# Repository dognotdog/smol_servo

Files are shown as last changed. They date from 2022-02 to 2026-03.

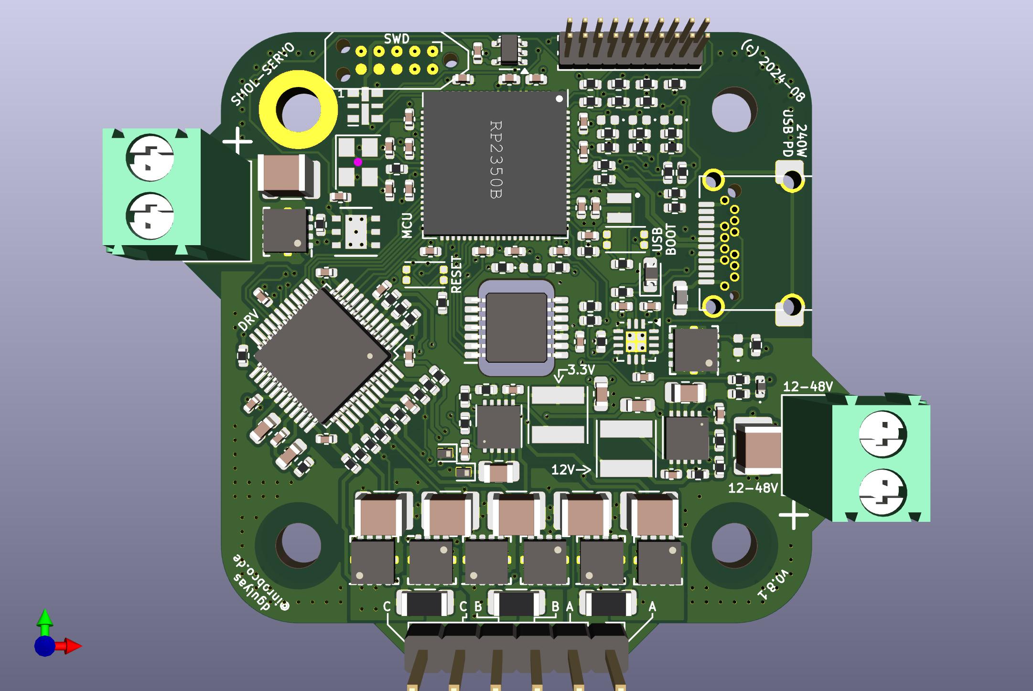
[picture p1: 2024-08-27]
hardware/smol-servo-rpi2350-tmc6200/smol-servo-rpi2350-tmc6200.jpg

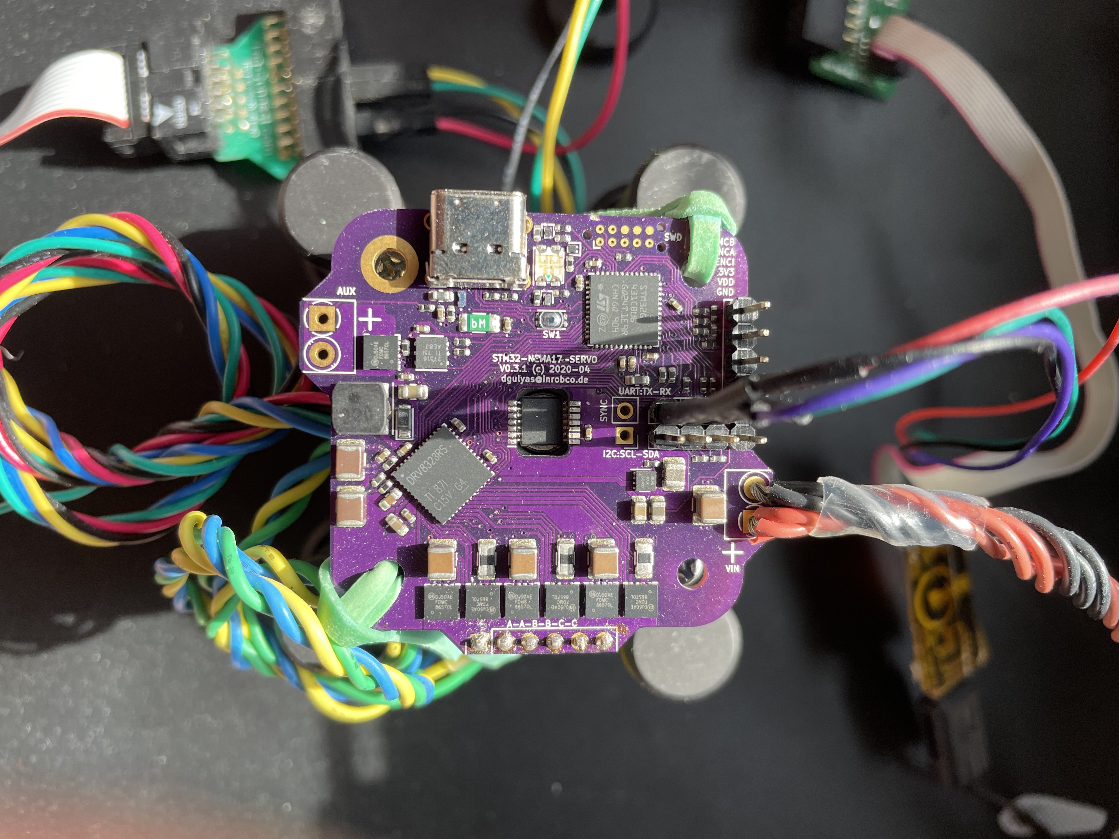
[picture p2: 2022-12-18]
doc/v0.3.1_proto.jpg

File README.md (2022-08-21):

# Project Layout

## firmware48

Contains files specific to 48pin STM32G431 on the stm32-nema17-servo board.

## mechaduino-firmware

Firmware for Mechaduino's SAMD21G18A Cortex M0+.

## hardware

Hardware design files for Schematic and PCB.

## tests

There is a basic harness in place to use [Unity](https://github.com/ThrowTheSwitch/Unity) for unit testing. Create `foo_test.c` modules for testing, and `foo_test.mk` makefiles for additional setup.

# Calculations

### Current Sense Shunt Resistor Value

Rated continous current 8A, max. Bus Voltage 50V, min. load 1R

 - 1206 can dissipate 1.5W usually, using a conservative 1W for the rated current: P/I^2 -> Rs < 15.6mOhm

With a 1R load on a 50V bus, up to 50A could flow at once, but hopefully motor inductance smoothes that out. Assuming 50kHz, 2mH winding inductance:
	V = L * di/dt -> di/dt = V/L = 25kA/s @ 50kHz = 0.5 A/cycle

### Gate Drive

The required charge pump current is
	I_VCP = 3 * Q_G * f_PWM.

DRV8323 charge pump VBUS limits:
6V -> 10mA
8V -> 15mA
10V -> 20mA
13V -> 25mA

#### NTTFS4937N

Q_G = 35.5 nC

I_VCP = 3.55 mA @ 100kHz
I_VCP = 1.78 mA @ 50kHz

Charge pump current capacity is well over required charge pump current.

#### FDMC86570L

Q_G < 88 nC

I_VCP = 8.8 mA @ 100kHz
I_VCP = 4.4 mA @ 50kHz

#### FDMC86183

Q_G ~ 15 nC
Q_gd ~ 3.4 nC

### Passive NSS OR circuit

3.3V, 5pF gate capacitance, 8mA sink/source per pin -> 412.5 Ohm minimum resistance

f_RC = 1 / 2pi R C

for R=470 that is 67.7MHz
for R=1k that is 31.8MHz
for R=2.2k that is 14.4MHz

max SPI frequency is 10MHz. 1k for both lines seems sufficiently fast and will not exceed max current on pin. Only one will be actively pulled high, the other will be in high impedance mode, but 1k is safe even if both are actively driven against the NSS pin.

# Electrical Motor Driving

## RL Circuit
The principal equation for an RL circuit, as is assumed for a motor winding, describing the relationship between voltage and current is:
`V = L * di/dt + R i`
or in differential form
```
	        V - R i
	di/dt = -------
	           L
```

### Discrete Time RL Equation

In discrete time, with n=0,1,2... indices going backward in time, the equation becomes
`V_0 = L * (i_0 - i_1) / T + R i_0`
solving for L
```
      V_0 - R i_0
L = T -----------
       i_0 - i_1
```
solving for R
```
    V_0 - L * (i_0 - i_1) / T
R = -------------------------
               i_0
```
assuming a measurement at n=0 for R and n=1 for L, and substituting
```
                V_0 - L * (i_0 - i_1) / T
      V_1 - i_1 -------------------------
                           i_0
L = T -----------------------------------
                 i_1 - i_2

      V_1 i_0 - i_1 V_0     i_1 (i_0 - i_1)
L = T ----------------- + L ---------------
       i_0 (i_1 - i_2)      i_0 (i_1 - i_2)        

               V_1 i_0 - i_1 V_0 
L = T ----------------------------------
       i_0 (i_1 - i_2) - i_1 (i_0 - i_1)        

      V_1 i_0 - i_1 V_0          i_0 - i_1
L = T ----------------- = T V ---------------
       i_1^2 - i_0 i_2        i_1^2 - i_0 i_2

          V_1 - R i_1
    V_0 - ----------- (i_0 - i_1)
           i_1 - i_2
R = -----------------------------
                i_0

    V_0 (i_1 - i_2) - V_1 (i_0 - i_1) + R i_1 (i_0 - i_1)
R = -----------------------------------------------------
                      i_0 (i_1 - i_2)

    V_0 (i_1 - i_2) - V_1 (i_0 - i_1)
R = ---------------------------------
    i_0 (i_1 - i_2) - i_1 (i_0 - i_1)

    V_0 (i_1 - i_2) - V_1 (i_0 - i_1)     2 i_1 - i_2 - i_0
R = --------------------------------- = V -----------------
             i_1^2 - i_0 i_2               i_1^2 - i_0 i_2

       L         i_0 - i_1
tau = --- = T -----------------
       R      2 i_1 - i_2 - i_0
```

# Stepper Control

A Bipolar hybrid stepper motor typically has 200 steps/rev on 2 phases.

An electrical revolution is four full steps: 
A+ -> B+ -> A- -> B-

NEMA 17 typically up to 3A current (eg. Nanotec ST4118D3004)""

winding current: 3A
winding inductance: 2.7mH 
winding resistance: 1.1R
Holding Torque: 0.8Nm
Rotor Inertia: 1.02e-5 Kg m^2
Torque Constant (mech): 0.267 Nm / A [or V / rad s]

At 48V, the motor should be able to spin (theoretically, discounting nonlinear effects) at 179.7 rad/s, about 1716 rpm or 28.6 rev/s.

at 30 rev/s with 200 steps/rev, we have to make 6000 full steps per second.

# BLDC Control

A BLDC has 3 phases, which are most simplistically driven with trapezoidal voltage curves instead of sinusoidal ones.
```
      _       _
A   /   \   /
  -       -
        _      
B \   /   \   /
    -       -
  _       _      
C   \   /   \   
      -       -
```

A ~ sin(alpha)
B ~ sin(alpha + 2pi/3)
C ~ sin(alpha + 4pi/3)

In a typical configuration, the three windings A,B,C are connected in a star pattern, with the endpoints named U,V,W.
```
V       U
B \   / A	    
    *       
    | C
    W
```
A = 

U-V 	= A
V-W 	= B-C = sin(a + 2pi/3) - sin(a + 4pi/3) 
	= sin(a) cos(2pi/3) + cos(a) sin(2pi/3) - sin(a) cos (4pi/3) - cos(a) sin(4pi/3)
	= sin(a) - sqrt(3) cos(a)
W-U = C-A

# STM32G431 Setup

## USB

Crystal-less USB Setup in MX
 - USB clock source should be `HSI48`1
 - set `CRS SYNC` to `USB_FS` in RCC Mode & Config
 - enable `Sof Enable` in USB device settings

Full-Speed USB (12Mbps) has a max. packet size of 64 bytes for regular packets, only isochronous might be up to 1023.

### CDC
 - increase `APP_RX_DATA_SIZE` and `APP_TX_DATA_SIZE` to at least 64
 - add at least 7 byte persistent buffer to store data from `CDC_SET_LINE_CODING` that can be output on `CDC_GET_LINE_CODING`

## Peripheral usage

ADC1: internal sensors, voltage reference
ADC2: CH3, CH13, CH17 inputs for current sense resistors, from V0.2 CH14 for VBUS sense

I2C3: I2C for communicating with the outside world
SPI2: connected to MOSFET driver and encoder ICs
USART1: external UART

TIM2: CH1 brake resistor, CH2,CH3,CH4 A,B,C PWM outputs for half bridges
TIM3: external quadrature encoder input
TIM4: CH1,CH2,CH3 LED RGB PWM output (CH4 connects to SYNC)
TIM6: Timer for performance counter with PSC=169 to get a 1us count resolution @ 170MHz clock

TIM1,TIM7,TIM8,TIM15,TIM16,TIM17: unused

# Blackmagic Probe debugging

Firmware update for probe:
`dfu-util -d 1d50:6018,:6017 -s 0x08002000:leave -D <blackmagic-native.bin>`

## GDB

```
~/Applications/ARM-Toolchain/gcc-arm-none-eabi-8-2019-q3-update/bin/arm-none-eabi-gdb
target extended-remote /dev/cu.usbmodem79A760B81
monitor swdp_scan
attach 1
```

# Board Revisions

## V0.6.0 (TMC6200)
 - C22 (0.022uF 100V) is not available in 0402, thus 2 10n caps in parallel have to be used, stacked on top of each other.

## V0.4

### Changes
 - Change to 4-layer board for better power planes, and to de-clutter some of the signal paths.
 - Change USB-C socket footprint to be compatible two variants

## V0.3.1

### Known Bugs
 - (16.b) no zeners on VBUS/VDDP monitor taps means no chip protection

### Bugfixes
 - (15) move motor connector out by another 25mil
 - (16.a) 100n cap instead of zeners on VBUS/VDDP give much better accuracy
 - (17) add ground traces for current sense amps

### Observations
 - (17) it looks as though A and C bridges are measuring current much closer together with the dedicated ground traces

## V0.3

### Known Bugs
 - (15) motor connector does not have enough clearance for connection from back
 - (16) adding small buffer caps (100n) on voltage dividers for VBUS/VDDP would help with inaccuracy due to high-impedance source.
 - (17) current sense traces are not routed differentially, need ground lines directly to sense resistors instead of via ground plane to prevent induced effects

### Bugfixes
 - (3) change footprint of L2 from 0806 to 1005
 - (10) connects DRV8323 VREF to 3V3 plane
 - (11) connects STM32G4 VREF to 3V3 plane
 - (12) correct B1/B12 spacing on USB-C receptacle footprint
 - (13) Change D3 to ABRG and switch B/G channels on STM32G4
 - (14) move VDDDIV to PF0-ADC1_IN10
 - (8) with VDDDIV moved, re-connected hardware NSS, as STM32G4 should be able to pulse it between frames for proper DMA transfers with NSSP enabled, and add passive OR-ing resistors so that chip can be selected.

### Enhancements
 - Add 500mA polyfuse to USB 5V input to protect the input diode (and host) in case of VDD short to ground
 - change D2 to bigger footprint to be able to fit bigger diode with appropriate voltage rating

### Software Differences

Correction: Hardware NSS does NOT work because it requires opposite clock signal polarity :/

Enable hardware NSS control as master with pulsing between data words

- hspi2.Init.NSS = SPI_NSS_SOFT;
+ hspi2.Init.NSS = SPI_NSS_HARD_OUTPUT;

- hspi2.Init.NSSPMode = SPI_NSS_PULSE_DISABLE
+ hspi2.Init.NSSPMode = SPI_NSS_PULSE_ENABLE

This enables use of DMA transfers for reading data from sensors.

## V0.2

### Known Bugs
 - (10) VREF pin of DRV8323 not connected to 3V3
 - (11) VREF pin of STM32G4 not connected to 3V3
 - (12) USB-C receptacle footprint slightly wrong, spacing of B1/B12 pins too narrow for easy fit
 - (13) Wrong Pinout for D3, was RGBA should be ABRG
 - (14) sensing VDD connected to PA15 doesn't work as PA15 can only be a trigger input, not an analog channel, PF0 is the only available pin with an analog channel on ADC1

### Bugfixes
 - (1): adds bus voltage analog input to PB11, moves DRVSEL to PB12 (nixing NSS, see (8))
 - (2): connect B4/B9 pins on USB connectors
 - (5): Q8/9/10 changed be GSD in schematic, as they should be for the SSM3K35CTC, resulting in 180deg rotation
 - (6): moved C3 a nudge further away from DM via
 - (7): force thermals on J4 and J5
 - (8) Remove U2 and DRVSCS/ASCS lines and replace them directly with DRVSEL/ASEL
 - (9) Add R30 as 10K pullup on MISO

### Enhancements

#### Additional VBUS Cap

Adds two additional 10uF capacitor to VBUS, for a total of 60uF capacitance. For a 50V bus, and a 1R load, which is 50A max current, and 50kHz PWM, that means a single full PWM cycle can drain `50*20e-6 = 1000 uC`. At 50v, the cap charge is 3000uC, so the bus voltage could still drop by nearly 20V without an external buffer cap.

Same load with 10V, it's a 10A max and thus only a 100uC discharge, which is a 2V drop, or again 20% of bus voltage.

VBUS caps have been relocated so that each FET pair gets one next to it, plus one at the VBUS input.

#### VDD and VBUS sense dividers

Sensing VBUS was added for controlling the brake resistor when the voltage rises too much.

Sensing VDD is for ...?

#### Portruding power connectors

Power connectors have been moved to portrude from the 42x42mm footprint, so that the board can be mounted on the back surface or very close to the back surface of a motor without the through-hole power connectors being in danger of touching the motor casing.

## V0.1

### Known Bugs
 - (1) No feedback of bus voltage to measure it, to be able to drive brake resistor accordingly
 - (2) USB B4 and B9 not connected
 - (3) L2 probbaly has too small a footprint (BRL3225T2R2M is too large, though seems to solder ok)
 - (4) stencil cutouts too small for the high density IC pins (vreg especially), not enough solder is on pins to make good contact on reflow
 - (5) LED driver transistors Q8/9/10 are pinned wrong, should be GSD for SSM3K35CTC
 - (6) C3's 3V3 pad too close to DM via, though boards seemed to have come out fine
 - (7) VBUS pad on J4 and OR pad on J5 connector have no thermals for hand-soldering
 - (8) SPI hardware is incapable of doing word-wise NSS triggering, thus the whole logic dance with U2 may not be necessary, as we can just do software SS from GPIO
 - (9) 10K pullup might be required for DRV8323 on MISO line
 - (10) VREF pin of DRV8323 not connected to 3V3
 - (11) VREF pin of STM32G4 not connected to 3V3
 - (12) USB-C receptacle footprint slightly wrong, spacing of B1/B12 pins too narrow for easy fit
 - (13) Wrong Pinout for D3, was RGBA should be ABRG

### Status

 - USB CDC output works
 - SPI to both AD5047D and DRV8323 work after fixing bug (9)
 - all power transistors are switched under a no load condition, with DRV8323 in 3xPWM mode

# Alternate Parts

## STM32G431CxU
G441, G491, GG4A1, G473, G483, G474, G484

### NRF5340

The nRF5340 is the successor of the nRF52 series, and is a dual-core design at 128MHz and 64MHz, respectively

#### ADC

The ADC can be configured for acquisition times between 3 and 40 us, with a minimum of 10us for VDD monitoring. The conversion time is 2us, giving us a max. sample rate of 200kHz

#### Timers / PWM

The timers only run at 16MHz, which at 100kHz would only give a resolution of 160 counts for a PWM signal. This is compared to the full 168MHz resolution of the STM32G4, giving 1680 counts, roughly 10x the resolution, for an effective 10 bits vs 7 bits.

### LPC5528JEV98K

An ARM Cortex M33 core @ 150MHz, in a 0.5mm pitch BGA package.

### ADuCM410

2 MSPS 16bit ADC, 160 MHz ARM Cortex M33, 5x5mm, 0.5mm pitch BGA

### ATSAM4S

120MHz ARM Cortex M4, no FPU though. 100pin BGA 7x7, 0.65mm pitch.

## DRV8323RS

This part has both the 3ph driver and current sense.

### DRV8353R

Higher voltage, similar part

### DRV8300NRGR + INAxxx

The DRV8300 needs extra current sense amplifiers and a high-side bootstrap, pluss VDD supply. Looks like INA190 or INA210 can do bidirectional sensing

### TMC6200

### FDMF2011

interesting integrated half bridge for up to 20A

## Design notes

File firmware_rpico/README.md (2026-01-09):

# Servo Controller Firmware for RP2350

## Target Features

 - high frequency servo loop
   - LQG linear quadratic gaussian control
   - motor param auto-identification
   - on-axis AD5047 magnetic encoder
   - external A/B incremental encoder
 - 3-phase bridge control
 - 2/3-phase bridge control: 2ph stepper on 3ph bridge
 - multi-axis sync
 - 240W USB PD (48V @ 5A) or stand-alone 12V-48V supply

## Hardware Mapping

### 3ph Bridge + Power Resistor

GPIO22 | PWM[3A] | PWMR 
GPIO24 | PWM[4A] | PWMA
GPIO25 | PWM[4B] | ENA
GPIO26 | PWM[5A] | PWMB
GPIO27 | PWM[5B] | ENB
GPIO32 | PWM[8A] | PWMC
GPIO33 | PWM[8B] | ENC

### 3ph Driver Comms

GPIO28 | DRV_MISO
GPIO29 | DRV_NSS
GPIO30 | DRV_SLCK
GPIO31 | DRV_MOSI

GPIO34 | DRVFAULT
GPIO35 | DRVEN

### 3ph Current Sense

GPIO40_ADC0 | SOA
GPIO41_ADC1 | SOB
GPIO42_ADC2 | SOC

### Voltage Sensing 

GPIO43_ADC3 | VBUS
GPIO44_ADC4 | VDD
GPIO45_ADC5 | ADCA
GPIO46_ADC6 | ADCB
GPIO47_ADC7 | ADCC

### AD5047 Magnetic Encoder

GPIO36 | MAG_MISO
GPIO37 | MAG_NSS
GPIO38 | MAG_SLCK
GPIO39 | MAG_MOSI

### Encoder Input

GPIO3 | ENCI
GPIO4 | ENCA
GPIO5 | ENCB

### AP2020 RGB LED

GPIO10 | LED_SCK
GPIO11 | LED_MOSI

### FUSB302 USB PD Controller

GPIO0 | USB_PD_SDA
GPIO1 | USB_PD_SCL
GPIO2 | USB_PD_INT

### Serial Console UART

GPIO6 | CONSOLE_TX
GPIO7 | CONSOLE_RX

### Aux Flash

GPIO23 | FLASH_SS

Data on QSPI_* pins.

### Other GPIO

GPIO8
GPIO9
GPIO12
GPIO13
GPIO14 | SDA1_EXT
GPIO15 | SCL1_EXT
GPIO16 | SYNC
GPIO17-21 is not connected

## Servo Loop Timing

Assuming `sysclk = 150MHz`, and 20kHz control loop, we should run PWM in up/down mode at 60kHz (3 phases * 20kHz) and do ADC reads at both counter TOP and 0 values. `TOP+1 = 1250` for `2*60 = 120kHz` operation.

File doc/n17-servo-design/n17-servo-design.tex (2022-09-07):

% !TEX TS–program = pdflatexmk
\documentclass[12pt,a4paper,oneside,openany]{article}
\usepackage[squaren]{SIunits}
%% LaTeX Preamble - Common packages
\usepackage[english]{babel}
\usepackage{setspace}

\usepackage{fancyhdr}
\pagestyle{fancy}
%\cfoot{\thepage{} – CONFIDENTIAL}

\usepackage[utf8]{inputenc} % Any characters can be typed directly from the keyboard, eg √©√ß√±
\usepackage{textcomp} % provide lots of new symbols
\usepackage{graphicx}  % Add graphics capabilities
\usepackage{flafter}  % Don't place floats before their definition
%\usepackage{topcapt}   % Define \topcaption for placing captions above tables (not in gwTeX)
%\usepackage{natbib} % use author/date bibliographic citations
%\usepackage{babelbib}
\usepackage[backend=biber]{biblatex}
\addbibresource{n17-servo-design.bib}

\usepackage{caption}
\usepackage{subcaption}
\usepackage{enumitem}

\usepackage{amsmath,amssymb}  % Better maths support & more symbols
\usepackage{bm}  % Define \bm{} to use bold math fonts
\usepackage{esint}
\usepackage{algorithm}
\usepackage{mathenv}
%\usepackage[noend]{algorithmic}
\usepackage{algorithmicx}
\usepackage{algpseudocode}
\usepackage[usenames,dvipsnames]{color} 

\usepackage[pdftex,bookmarks,colorlinks,breaklinks]{hyperref}  % PDF hyperlinks, with coloured links
%\definecolor{dullmagenta}{rgb}{0.4,0,0.4}   % #660066
%\definecolor{darkblue}{rgb}{0,0,0.4}
\hypersetup{linkcolor=red,citecolor=blue,filecolor=blue,urlcolor=blue} % coloured links
%\hypersetup{linkcolor=black,citecolor=black,filecolor=black,urlcolor=black} % black links, for print output

\usepackage{memhfixc}  % remove conflict between the memoir class & hyperref
% \usepackage[activate]{pdfcprot}  % Turn on margin kerning (not in gwTeX)
%\usepackage{pdfsync}  % enable tex source and pdf output syncronicity

\usepackage{longtable}
\usepackage{booktabs}
\usepackage{listings}
\usepackage{nomencl}
\usepackage{todonotes}

\usepackage[noabbrev]{cleveref}

\usepackage{tablefootnote}
%\makesavenoteenv{tabular}

%\usepackage{pinoutikz}
%\usepackage{xparse}

\usepackage{tikz}
\usetikzlibrary{calc,arrows,through,backgrounds,fit,shapes.geometric,shapes.misc,plotmarks,positioning,trees,decorations.pathmorphing,decorations.markings,patterns}
% external lib for caching graphics
\usetikzlibrary{external}
\usepackage{circuitikz}
\usepackage{pgfplots}
\usepgfplotslibrary{external}
\tikzexternalize[prefix=tikz/]

%\usepackage{sagetex}

%\usepackage{anysize}
%\marginsize{2cm}{2cm}{2cm}{2cm}

\onehalfspacing

\makenomenclature
\def\nomlabel#1{\textbf{#1}\hfil}

%\newcommand{\Parameters}{\subsection*{Parameters}}
%\newcommand{\ReturnValue}{\subsection*{Return Value}}
%\newcommand{\Description}{\subsection*{Description}}
%\newcommand{\ClassName}[1]{{\tt #1}}
%\newcommand{\ReturnType}[1]{{\tt (#1)}}
%\newcommand{\Function}[1]{{\tt #1()}}
%\newcommand{\Self}{{\tt self}}

\DeclareMathOperator{\ud}{d}
\DeclareMathOperator{\udt}{\frac{d}{dt}}
%\DeclareMathOperator{\udtt}{\frac{\ud^2}{\ud t^2}}
\DeclareMathOperator{\rank}{rank}
\DeclareMathOperator{\fclamp}{clamp}
\DeclareMathOperator{\fsign}{sign}
%\newcommand{\ud}{\ensuremath{\binop{\mathrm{d}}}}
\newcommand{\vx}{\ensuremath{\mathbf{x}}}
\newcommand{\vy}{\ensuremath{\mathbf{y}}}
\newcommand{\vz}{\ensuremath{\mathbf{z}}}
\newcommand{\vu}{\ensuremath{\mathbf{u}}}
\newcommand{\vv}{\ensuremath{\mathbf{v}}}
\newcommand{\vw}{\ensuremath{\mathbf{w}}}
\newcommand{\va}{\ensuremath{\mathbf{a}}}
\newcommand{\vf}{\ensuremath{\mathbf{f}}}
\newcommand{\vh}{\ensuremath{\mathbf{h}}}
\newcommand{\vt}{\ensuremath{\mathbf{t}}}
\newcommand{\vk}{\ensuremath{\mathbf{k}}}
\newcommand{\mM}{\ensuremath{\mathbf{M}}}
\newcommand{\mW}{\ensuremath{\mathbf{W}}}
\newcommand{\mJ}{\ensuremath{\mathbf{J}}}
\newcommand{\mA}{\ensuremath{\mathbf{A}}}
\newcommand{\mB}{\ensuremath{\mathbf{B}}}
\newcommand{\mH}{\ensuremath{\mathbf{H}}}
\newcommand{\vq}{\ensuremath{\mathbf{q}}}
\newcommand{\mC}{\ensuremath{\mathbf{C}}}
\newcommand{\mK}{\ensuremath{\mathbf{K}}}
\newcommand{\mP}{\ensuremath{\mathbf{P}}}
\newcommand{\mQ}{\ensuremath{\mathbf{Q}}}
\newcommand{\mR}{\ensuremath{\mathbf{R}}}
\newcommand{\mS}{\ensuremath{\mathbf{S}}}
\newcommand{\vlambda}{\ensuremath{\boldsymbol{\lambda}}}
\newcommand{\vd}{\ensuremath{\mathbf{d}}}
\newcommand{\mI}{\ensuremath{\mathbf{I}}}
\newcommand{\vc}{\ensuremath{\mathbf{c}}}
\newcommand{\vr}{\ensuremath{\mathbf{r}}}
\newcommand{\vF}{\ensuremath{\mathbf{F}}}
\newcommand{\vtau}{\ensuremath{\boldsymbol{\tau}}}
\newcommand{\valpha}{\ensuremath{\boldsymbol{\alpha}}}

\newtheorem{mydef}{Definition}

\lstset{numbers=left,basicstyle=\footnotesize\ttfamily,numberstyle=\tiny,tabsize=4,breaklines=true}
\lstset{language=[Objective]C}
\lstset{commentstyle=\color{BrickRed}\itshape,
	keywordstyle=\color{RoyalBlue}\bfseries,
	identifierstyle=\color{Blue},
	stringstyle=\color{Gray}}

\long\def\symbolfootnote[#1]#2{\begingroup%
\def\thefootnote{\fnsymbol{footnote}}\footnote[#1]{#2}\endgroup}

\begin{document}

\title{Servo Controller Design Notes}
\author{Dömötör Gulyás\\v0.1}

\maketitle

%\abstract
%
%foopsum.
%
%

\tableofcontents

%\listoffigures

%\section{Introduction}

%\begin{figure}[htbp]
%\begin{center}
%\includegraphics[scale=0.8]{n17-servo-pwm-adc.pdf}
%\caption[Fig]{foo}
%\label{fig:pwm-adc}
%\end{center}
%\end{figure}

\section{TODO}

\subsection{Flux-braking}
\href{https://en.wikipedia.org/wiki/Braking_chopper#Flux_braking}{https://en.wikipedia.org/wiki/Braking\_chopper\#Flux\_braking}

\section{Hardware}

The hardware is laid out to be as flexible as possible, driving both 3-phase BLDC and servo motors, as well as 2-phase steppers.

3 half bridges with discrete transistors allow high currents. The DRV8323 stepper driver works at up to 60V. The hardware is laid out for 12V-48V nominal voltage, but allowing 60V peak.

Using a 2-phase motor in this configuration limits the top speed due to lower effective voltage than one could get using 2 full bridges.

The main MCU is an STM32G431.

\subsection{SPI}

Unfortunately the STM32G4 SPI implementation does not allow hardware NSS signaling, as the SPI mode that needs to be used with the attached SPI devices (low clock polarity, latch on 2nd edge) is not compatible with hardware pulsing of NSS between data frames.

\subsection{MCU Peripheral Assignments}

\begin{table}[htbp]
\caption{MCU Peripheral Usage}
\begin{center}
\begin{tabular}{ll} \toprule
 Peripheral & Usage \\
\midrule \texttt{ADC1} & Auxiliary analog inputs \\
\texttt{ADC2} & Current Sensing \\
\midrule
\texttt{TIM1} & Event counter for debugging \\
\texttt{TIM2} & PWM Gate Driver (R,A,B,C) \\
\texttt{TIM3} & Encoder Input \\
\texttt{TIM4} & RGB LED PWM + SYNC\\
\texttt{TIM6} & Performance Counter / Timer \\
\texttt{TIM15} & current sense trigger offset \\
\texttt{TIM16} & SPI NSS pulse timer \\
\midrule
\texttt{I2C3} & I2C I/O \\
\texttt{USART1} & Debug I/O \\ 
\texttt{SPI2} & Gate Driver and Magnetic Encoder \\
\texttt{USB} & USB Interface \\
\bottomrule
\end{tabular}
\end{center}
\label{tab:mcu-peripherals}
\end{table}%

\begin{figure}[htbp]
\begin{center}
\begin{tikzpicture}[scale=0.38,
     pin/.style={draw,rectangle,minimum width=1.8em}
     ]
   % Main trick: loop over the label numbers and then adjust their position
   % in the tikzpicture using evaluate to calculate \y=y-coordinate of pin
   \foreach \i/\desc [evaluate=\i as \y using (1.5*(-\i+6.5))]
      in {1/{3V3},
          2/{$\times$},
          3/{$\times$},
          4/{$\times$},
          5/{ADC1\_IN10},
          6/{$\times$},
          7/{RST},
          8/{TIM2\_CH1},
          9/{TIM2\_CH2},
         10/{TIM2\_CH3},
         11/{TIM2\_CH4},
         12/{ADC2\_IN17} }
   {
     \draw node[pin,anchor=west] at (-12,\y){$\i$}; % pin
     \node[align=right,anchor=east] at (-12,\y){\desc}; % description
   }
   \foreach \i/\desc [evaluate=\i as \x using (1.5*((\i-12)-6.5))]
     in {13/{ADC2\_IN13},
         14/{ADC2\_IN3},
         15/{PA7},
         16/{PC7},
         17/{PB0},
         18/{PB1},
         19/{PB2},
         20/{VREF+},
         21/{VDDA},
         22/{PB10},
         23/{VDD},
         24/{ADC1\_IN14} }
   {
     \draw node[pin,anchor=west,rotate=90] at (\x,-12){\small$\i$};
     \node[align=right,anchor=east,rotate=90] at (\x,-12){\desc};
   }
   \foreach \i/\desc [evaluate=\i as \y using (1.5*((\i-24) - 6.5)]
     in {25/{NSS},
         26/{SCK},
         27/{MISO},
         28/{MOSI},
         29/{PC6},
         30/{SCL},
         31/{TX},
         32/{RX},
         33/{DM},
         34/{DP},
         35/{VDD},
         36/{SWDIO} }
   {
     \draw node[pin,anchor=east] at (12,\y){$\i$};
     \node[align=left,anchor=west] at (12,\y){\desc};
   }
   \foreach \i/\desc [evaluate=\i as \x using (1.5*(6.5-(\i-36)))]
     in {37/{SWDCLK},
         38/{$\times$},
         39/{$\times$},
         40/{SDA},
         41/{TIM3\_ETR},
         42/{TIM3\_CH1},
         43/{TIM3\_CH2},
         44/{TIM4\_CH1},
         45/{TIM4\_CH2},
         46/{TIM4\_CH3},
         47/{TIM4\_CH4},
         48/{VDD} }
   {
     \draw node[pin,anchor=east,rotate=90] at (\x,12){$\i$};
     \node[align=right,anchor=west,rotate=90] at (\x,12){\desc};
   }
%   \draw[ultra thick]
%      (0,0.8)--(0,17.2)--(0.8,18)--(17.2,18)--(18,17.2)
%             --(18,0.8)--(17.2,0)--(0.8,0)--cycle;
   \draw[ultra thick]
      (-12,-12)--(-12,12)--(12,12)
             --(12,-12)--cycle;
   \draw(-9,9)circle[radius=0.7];
   \node (mcu) at (0,0){STM32G4};
   \node[below=of mcu]{QFN48};
 \end{tikzpicture}
\caption[RL Circuit]{STM32G4 pinout diagram.}
\label{fig:stm-pinout}
\end{center}
\end{figure}

\begin{longtable}[htbp]{@{}rlll@{}}%
\caption{STM32G431 pin assignments for hardware version 0.3. \label{tab:mcu-pins}} \\
\toprule 
        Pin & GPIO         & Peripheral        & Usage \\
\midrule 
\endfirsthead
%\midrule
\multicolumn{4}{c}{\ldots table continued from previous page} \\
\midrule
         Pin & GPIO         & Peripheral        & Usage \\
\midrule
\endhead
\multicolumn{4}{c}{table continues on next page \ldots} \\
%\midrule
\endfoot
\bottomrule
\endlastfoot
          1 & \texttt{VBAT} &                   & \texttt{3V3}  \\
\midrule  5 & \texttt{PF0}  &\texttt{ADC1 IN10} & VDDP sensing \\
\midrule  7 & \texttt{PG10} &                   & reset input \\
\midrule  8 & \texttt{PA0}  &\texttt{TIM2 CH1}  & Brake Resistor PWM \\
          9 & \texttt{PA1}  &\texttt{TIM2 CH2}  & Channel A PWM \\
         10 & \texttt{PA2}  &\texttt{TIM2 CH3}  & Channel B PWM \\
         11 & \texttt{PA3}  &\texttt{TIM2 CH4}  & Channel C PWM \\
\midrule 12 & \texttt{PA4}  &\texttt{ADC2 IN17} & Current Sense Channel A \\
         13 & \texttt{PA5}  &\texttt{ADC2 IN13} & Current Sense Channel B \\
         14 & \texttt{PA6}  &\texttt{ADC2 IN3}  & Current Sense Channel C \\
\midrule 15 & \texttt{PA7}  &                   & DRV8323 Enable \\
\midrule 16 & \texttt{PC4}  &                   & DRVFAULT input \\
\midrule 17 & \texttt{PB0}  &                   & Enable Driver Channel C \\
         18 & \texttt{PB1}  &                   & Enable Driver Channel B \\
         19 & \texttt{PB2}  &                   & Enable Driver Channel A \\
\midrule 22 & \texttt{PB10} &                   & SPI Select AS5047 \\
\midrule 24 & \texttt{PB11} &\texttt{ADC1 IN14} & VBUS sensing \\
\midrule 25 & \texttt{PB12} &\texttt{SPI2 NSS}  &  \\
         26 & \texttt{PB13} &\texttt{SPI2 SCK}  &  \\
         27 & \texttt{PB14} &\texttt{SPI2 MISO} &  \\
         28 & \texttt{PB15} &\texttt{SPI2 MOSI} &  \\
\midrule 29 & \texttt{PC6}  &                   & SPI Select DRV8323 \\

\midrule 30 & \texttt{PA8}  &\texttt{I2C3 SCL}  & \\
\midrule 31 & \texttt{PA9}  &\texttt{UART1 TX}  & Debug TX \\
         32 & \texttt{PA10} &\texttt{UART1 RX}  & Debug RX \\
\midrule 33 & \texttt{PA11} &\texttt{USB DM}    & \\
         34 & \texttt{PA12} &\texttt{USB DP}    & \\
\midrule 36 & \texttt{PA13} &\texttt{SWD SWDIO} & \\
         37 & \texttt{PA14} &\texttt{SWD SWCLK} & \\
\midrule 40 & \texttt{PC11} &\texttt{I2C3 SDA}  & \\
\midrule 41 & \texttt{PB3}  &\texttt{TIM3 ETR}  & External Encoder I\\
         42 & \texttt{PB4}  &\texttt{TIM3 CH1}  & External Encoder A\\
         43 & \texttt{PB5}  &\texttt{TIM3 CH2}  & External Encoder B\\
\midrule 44 & \texttt{PB6}  &\texttt{TIM4 CH1}  & LED Red \\
         45 & \texttt{PB7}  &\texttt{TIM4 CH2}  & LED Green \\
         46 & \texttt{PB8}  &\texttt{TIM4 CH3}  & LED Blue \\
         47 & \texttt{PB9}  &\texttt{TIM4 CH4}  & SYNC I/O \\
%\bottomrule
\end{longtable}

\section{PWM and Current Sensing}

%\begin{figure}[htbp]
%\begin{center}
%\includegraphics[scale=0.4]{n17-servo-pwm-adc.pdf}
%\caption[PWM and ADC Sync]{Temporal synchronization of PWM output and ADC sampling.}
%\label{fig:pwm-adc}
%\end{center}
%\end{figure}

\subsubsection{ADC Triggering}

As the ADC sampling takes a finite time, it will not quite sample on-center. \texttt{TIM15} is setup to offset by $T_{\textrm{base}} - T_{\textrm{ssaa}}/2$.\footnote{$\unit{6.47}{\micro\second}$ or 1100 CPU cycles for 1700 cycle period.}

\begin{figure}[htbp]
\begin{center}

\caption[PWM and ADC Sync with Offset]{Temporal synchronization of PWM output and ADC sampling with centering offset. Adding a triggered timer  (\texttt{TIM15}) as a delay allows offsetting the ADC sampling to occur centered on PWM phases.}
\label{fig:pwm-adc-offset}
\end{center}
\end{figure}

\subsection{Sense Resistor Choice}

The \em DRV8323 \em has a programmable gain between 5 and 40, with 20 being the default. 1206-size resistors can dissipate \unit{1}{\watt}\footnote{\unit{2-3}{\watt} according to datasheets for different resistors, so this is with adequate margin}. For \unit{8}{\ampere}, $P = \unit{0.96}{\watt}$ with $R=\unit{15}{\milli\ohm}$. The sense amplifiers can go up to \unit{0.25}{\volt} short of the supply rails, for a \unit{3.3}{\volt} that leaves \unit{\pm 1.4}{\volt}. The sense voltage $U_S \ @ \  \unit{8}{A}=\unit{120}{\milli\volt}$, thus a gain factor of 5 or 10 would cover the expected current range nicely.

The sense resistor could be made be smaller to reduce power dissipation and allow higher curents, at the expense of reduced resolution.

%// 	// default amp gain factor is G = 20 (5/10/20/40) are available
%// 	// current sense shunts are Rs = 15mOhm
%// 	// sense amp output is centered on VREF/2, max. 0.25V away from rail
%// 	// thus +- 1.4V usable range
%// 	// for 12V operation, 10A would give 150mV, factor of 10 gives full range for 8A
%// 	// return Rs * G

\section{PWM}

The PWM output has to be synchronized with sampling the current sense values. This is done through builtin hardware trigger mechanisms between the different peripherals on the MCU which allow precise timing without CPU involvement.

ADC sampling should happen in the middle of the PWM high/low periods, and to achieve this PWM is run in up/down counting mode, and the ADC readout is triggered at the end of each period.

The PWM base period $T_{\textrm{base}} = \unit{10}{\micro\second}$ ($f_{\textrm{base}} = \unit{100}{\kilo\hertz}$) results in an effective output period of $T_{\textrm{gate}} = \unit{20}{\micro\second}$ ($f_{\textrm{gate}} = \unit{50}{\kilo\hertz}$), and ADC sampling of each channel every $T_{\textrm{sense}} = \unit{60}{\micro\second}$ ($f_{\textrm{sense}} = \unit{16.7}{\kilo\hertz}$). \unit{16.7}{\kilo\hertz} leaves \unit{10.2}{\kilo} instruction cycles per control loop iteration.\footnote{The base frequency could be increased to \unit{120}{\kilo\hertz}, to get $f_{\textrm{ctrl}} = \unit{20}{\kilo\hertz}$. Increasing the PWM frequency does reduce the effective resolution, and reduces the number of available instruction cycles (\unit{8.5}{\kilo} @ \unit{20}{\kilo\hertz}).}

\texttt{TIM2} is setup for driving the gate driver and brake resistor PWM.

\section {ADC}

\subsection{ADC Sampling Low-side Sense Resistor}

\begin{figure}[htbp]
\begin{center}
\begin{circuitikz} 
\ctikzset{diodes/scale=0.7}
% voltage source
\draw
  (3,-1) -- ++(-3,0) to[european voltage source, v=$U_{\textrm{bus}}$] (0,4) to ++(3,0)
  ;
% diodes
\draw
  (3,0) -- ++(0,0.25)  -- ++(-0.5,0) to[D,l=lo] ++(0,1.5) -- ++(0.5,0) to[short, -*] ++(0.0,0.25)
  -- ++(0,0.25) -- ++(-0.5,0) to[D,l=hi] ++(0,1.5) -- ++(0.5,0) -- ++(0,0.25)
  ;
% switches
\draw
  (3.0,0.25) to[short,*-] ++(0.5,0)
  to[normal open switch] ++(0,1.5) to[short, -*] ++(-0.5,0)
;
\draw
  (3,2.25) to[short,*-] ++(0.5,0)
  to[closing switch] ++(0,1.5) to[short, -*] ++(-0.5,0)
;
% sense resistor
\draw
  (3,-1) to[R,resistors/scale=0.5,l=$R_{\textrm{sense}}$] ++(0,1)
;
% output node
\draw
  (3,2.0) to[short,-o] node[anchor=south west]{$U=U_{\textrm{bus}}$}(4.0,2.0)
;
\end{circuitikz}
\caption[RL Circuit]{Simplified half-bridge with body diodes and current sense resistor, high-side switch closed.}
\label{fig:halfbridge-diodes}
\end{center}
\end{figure}

\Cref{fig:halfbridge-diodes} illustrates why current cannot flow through $R_{\textrm{sense}}$ when the high-side switch is closed: closing the switch shorts $U$ to $U_{\textrm{bus}}$, thus precluding any current from flowing through the low-side body diode.

With super-sampling, the lack of current flow through the sense resistor while the high-side switch is on must be accounted for. 

\subsection{ADC Sampling Load-side Sense Resistor}

\begin{figure}[htbp]
\begin{center}
\begin{circuitikz} 
\ctikzset{diodes/scale=0.7}
% voltage source
\draw
  (3,0) -- ++(-3,0) to[european voltage source, v=$U_{\textrm{bus}}$] (0,4) to ++(3,0)
  ;
% diodes
\draw
  (3,0) -- ++(0,0.25)  -- ++(-0.5,0) to[D,l=lo] ++(0,1.5) -- ++(0.5,0) to[short, -*] ++(0.0,0.25)
  -- ++(0,0.25) -- ++(-0.5,0) to[D,l=hi] ++(0,1.5) -- ++(0.5,0) -- ++(0,0.25)
  ;
% switches
\draw
  (3.0,0.25) to[short,*-] ++(0.5,0)
  to[normal open switch] ++(0,1.5) to[short, -*] ++(-0.5,0)
;
\draw
  (3,2.25) to[short,*-] ++(0.5,0)
  to[closing switch] ++(0,1.5) to[short, -*] ++(-0.5,0)
;
% sense resistor
\draw
  (3,2.0) -- ++(1,0) to[R,resistors/scale=0.5,l=$R_{\textrm{sense}}$,-o] ++(1.0,0.0) node[anchor=west]{$U$}
;
%% output node
%\draw
%  (5.0,2.0) to[short,-o] node[anchor=south west]{$U=U_{\textrm{bus}}$} ++(1.0,0.0)
%;
\end{circuitikz}
\caption[RL Circuit]{Simplified half-bridge with body diodes and load-side current sense resistor, high-side switch closing.}
\label{fig:halfbridge-diodes-load}
\end{center}
\end{figure}

With the sense resistor on the load, common-mode rejection becomes important, and the sense amplifiers need time to settle after a switching event before measurements can be taken.

\subsection{Sampling High-Impedance Sources}

High-impedance voltage dividers will be affected by ADC input impedance. Longest possible sampling times and additional buffer capacitors at the input are advised.

\subsection{DRV8323}

The DRV83223 has low-side sense resistors.

\texttt{ADC2} is setup to sample with a 12.5 cycle sample time, with 16x oversampling. $f_{\textrm{ADC}} = \unit{170/3}{\mega\hertz}$, and a single channel takes $12.5+12.5$ cycles per sample\footnote{sampling plus conversion}, with $T_{\textrm{sample}} = \unit{0.44}{\micro\second}$. That ends up being $T_{\textrm{CONVx16}} = \unit{7.06}{\micro\second}$ with 16x oversampling, which means that one of the two sample periods should always fall into a switch-free period.

\subsubsection{TMC6200}

The TMC6200 has load-side sense resistors.

With the TMC6200, a wait of \unit{2-4}{\micro\second} needs to be performed after each switching event before sampling the respective current sense amplifier output.

Additionally, sampling spikes can be observed in the amplifier output, indicating about a \unit{140}{\milli\volt} drop with a \unit{12.5}{\nano\second} sample period.

With a \unit{10}{\micro\second} PWM period, the $T_{\textrm{CONVx16}} = \unit{7.06}{\micro\second}$ time is just above the necessary threshold, so the ADC needs to be run to result in $T_{\textrm{CONV}} < \unit{6}{\micro\second}$. Shifting to a \unit{24.5}{cycle} sample period, and 8x oversampling, $T_{\textrm{CONVx8}} = \unit{5.23}{\micro\second}$ should work nicely, though care must be taken to shift the sampling accordingly, too, to ignore the settling period.

Additionally, it looks like there is significant residual common-mode signal, which shows up as a difference between high and low-side offsets.

\section{AS5047D Magnetic Encoder on Shaft}

The AS5047D is optionally located in the center of the board, for a direct on-axis configuration. It is a 14-bit magnetic encoder. We use it via its SPI interface. The SPI angle data is updated at \unit{4}{\mega\hertz}.

Propagation delay of sensor is spec'd at \unit{100}{\micro\second} $\pm\unit{10}{\micro\second}$ from sensing to read via SPI. At \unit{8}{\mega\hertz}, SPI read of 16bits takes \unit{2}{\micro\second} nominally, so $\approx\unit{10}{\micro\second}$ for the 4x16bit words seems a reasonable assumption.

The AS5047 clocks out a response at the NEXT 16bit transfer. NSS needs to be asserted during each transfer. SPI $\texttt{CPOL}=0$, and $\texttt{CPHA}=1$, eg. clock is default low, and data is sampled on the falling edge. Unfortunately the STM32G4 SPI peripheral is incapable of asserting NSS via hardware. 

During regular operation, the angle reads can be pipelined, and should be timed to match PWM output and ADC readings. Operating at a \unit{50}{\kilo\hertz} PWM rate means a \unit{20}{\micro\second} period. 

\subsection{AS5047D Readout}

The AS5047D is read out via SPI. It is specified at a \unit{250}{\nano\second} refresh rate at SPI (\unit{4}{\mega\hertz}), with a \unit{90-110}{\micro\second} measurement delay. 

During normal operation, the encoder would be read out once per control cycle. A BLDC may rotate at up to 4000rpm, which is ~67rev/sec, or 419rad/sec. At 20kHz, that's about 9 degrees of rotation.

\subsubsection{Hardware timed SPI reads}

Unfortunately, a native hardware NSS trigger isn't quite possible, but a timer should still be able to trigger the NSS GPIO pin, and then kick off the SPI transfer. The \texttt{TIM2\_TRGO} signal from the \texttt{TIM2\_UP} event is used to center ADC reads, and could also be used to trigger the SPI reads.

The STM32G4 does not have the capability to trigger multiple DMA transfers from the same event, but events can be chained.

\begin{enumerate}
\item Assert encoder NSS (active low)
    \begin{enumerate}
    \item start counter and DMA transfer to GPIO bit clear register
    \item start counter \texttt{TIM8\_CH1}
    \item in one-pulse mode, count a few cycles (AS5047D requires \unit{350}{\nano\second} hold time before clocking, approx. 60 cycles @ \unit{170}{\mega\hertz}) until \texttt{TIM8\_CH1}
    \end{enumerate}
\item Clock out 16bits, read/write
    \begin{enumerate}
    \item start DMA data transfer on \texttt{TIM8\_CH1} (eg. after the timer counted long enough to have the chip select asserted)
    \end{enumerate}
\item Deassert NSS
    \begin{itemize}
    \item Either use \texttt{SPI2\_TX} DMA request as chained source for \texttt{DMA\_GENERATOR0}, which will set the NSS line high again.
    \item Or set NSS high from TX complete interrupt, as exact timing is uncritical, as long as it happens before the next \texttt{TIM2\_UP} event.
    \end{itemize}
\end{enumerate}

\begin{figure}[htbp]
\begin{center}
\begin{tikzpicture}[>=latex]
%    \draw (0,0) circle (3);
% times
	\draw[-,ultra thin] (0.0,1.25) -- ++(0,-3.5);
	\draw[<->] (0,1.0) node[anchor=east] {$T_{\textrm{ADC}}$} -- ++(9.0,0);
	\draw[-,ultra thin] (9.0,1.25) -- ++(0,-3.5);
	\draw[<->] (0,0.5) node[anchor=east] {$T_{\textrm{PWM}}$} -- ++(3.0,0);
	\draw[-,ultra thin] (3.0,0.75) -- ++(0,-3.0);
	\draw[-,ultra thin] (6.0,0.75) -- ++(0,-3.0);
	\draw[<->] (0,0.0) node[anchor=east] {$T_{\textrm{base}}$} -- ++(1.5,0);
	\draw[-,ultra thin] (1.5,0.25) -- ++(0,-2.5);
	\draw[-,ultra thin] (4.5,0.25) -- ++(0,-2.5);
	\draw[-,ultra thin] (7.5,0.25) -- ++(0,-2.5);
	\draw[-,ultra thin] (10.5,0.25) -- ++(0,-2.5);
	
	% pwm counter
	\draw[-,ultra thin] (-0.25,-2.0) -- ++(11,0);
	\draw[-,ultra thin] (-0.25,-0.5) -- ++(11,0);
	\draw[-,thick] (0,-2.0) -- ++(1.5,1.5) -- ++(1.5,-1.5) -- ++(1.5,1.5) -- ++(1.5,-1.5) -- ++(1.5,1.5) -- ++(1.5,-1.5) -- ++(1.5,1.5);
	\draw[] (0.0,-1.25) node[anchor=east] {$\texttt{COUNT}$};

	% TIM2
	\node (TIM2) at (0,-3.5) {};
	
  	\draw[-,ultra thin] ($(TIM2) + (0,0.75)$) -- ++(0,-1.0);
	\foreach \x in {1,...,7} 
  		\draw[-,ultra thin] ($(TIM2) + (1.5*\x,0.75)$) -- ++(0,-0.75);
	\draw[-,ultra thin] (-0.25,-3.0) -- ++(11,0);
	\draw[-,ultra thin] (-0.25,-3.5) -- ++(11,0);
	\draw[] (0.0,-3.25) node[anchor=east] {$\texttt{TIM2\_TRGO}$};
	\draw[-,thick,dash pattern=on 2pt off 1.5pt] (0,-3.0) -- ++(0,-0.5) -- ++(1.5,0);
	\foreach\x in {1,...,6} 
  		\draw[-,thick] (1.5*\x,-3.0) -- ++(0,-0.5) -- ++(1.5,0);

	% DMA GPIO
	\node (DMA_GPIO) at (0,-5.0) {};
	\draw ($(DMA_GPIO) + (0.0, 1.0)$) node[anchor=west] {Assert NSS.};
	\foreach \x in {0,...,7} 
  		\draw[-,ultra thin] ($(DMA_GPIO) + (1.5*\x,0.75)$) -- ++(0,-1.0);
	\draw[-,ultra thin] ($(DMA_GPIO) + (-0.25,0.0)$) -- ++(11,0);
	\draw[-,ultra thin] ($(DMA_GPIO) + (-0.25,0.5)$) -- ++(11,0);
	\draw[] ($(DMA_GPIO) + (0,0.25)$) node[anchor=east] {$\texttt{DMA\_GPIO}$};
	\filldraw[thick,fill=black!10!white,draw=black] ($(DMA_GPIO) + (1.5,0.5)$) rectangle ++(0.25,-0.5);

	% TIM8
	\node (TIM8) at (0,-6.5) {};
	\draw ($(TIM8) + (0.0, 1.0)$) node[anchor=west] {Count $t_{\textrm{L}}$.};
	\foreach \x in {0,...,7} 
  		\draw[-,ultra thin] ($(TIM8) + (1.5*\x,0.75)$) -- ++(0,-1.0);
	\draw[-,ultra thin] ($(TIM8) + (-0.25,0.0)$) -- ++(11,0);
	\draw[-,ultra thin] ($(TIM8) + (-0.25,0.5)$) -- ++(11,0);
	\draw[] ($(TIM8) + (0,0.25)$) node[anchor=east] {$\texttt{TIM8\_CH1}$};
	\filldraw[thick,fill=black!10!white,draw=black] ($(TIM8) + (1.5,0.5)$) rectangle ++(0.5,-0.5);

%   	\draw[->,dotted] (-3,0) -- (3,0); % node[anchor=west] {re};
%   	\draw[->,dotted] (0,-3) -- (0,3); % node[anchor=south] {im};
%   	\draw[->] (0,0) -- (30:3) node[anchor=210] {d};
%   	\draw[->] (0,0) -- (120:3) node[anchor=300] {q};
%    \draw[->]  (0:2.7)  node[anchor=315]{$\theta$} arc (0:30:2.7);
%    \draw[->, thick,dashed]  (0,0) -- (30:2.5) node[anchor=300] {$E$};
%    \draw[->, thick,dashed]  (0,0) -- (120:2.5) node[anchor=210] {$\tau$};
%    \draw[->, very thick]  
%        (30:0.5) coordinate (D)
%        (120:1.5) coordinate (Q)
%    	(0,0) -- (D) node[anchor=300] {$i_d$}
%    	(0,0) -- (Q) node[anchor=210] {$i_q$}
%    	(0,0) -- ($(D) + (Q)$) node[anchor=south] {$i$}
%	;
%    \draw[->, very thick]  (0,0) -- (30:0.75) node[anchor=south] {$I_d$};
%    \draw[->, very thick]  (0,0) -- (120:2) node[anchor=0] {$I_q$};
%    \draw[->, very thick]  (0,0) -- ($(30:0.75) + (120:2)$) node[anchor=south] {$I$};
%    \draw[-, dotted]  (30:0.75) -- ($(30:0.75) + (120:2)$) -- (120:2);

\end{tikzpicture}
\caption[AS5047D SPI]{SPI readouts.}
\label{fig:as5047d-spi}
\end{center}
\end{figure}

\section{The RL-Circuit}

\begin{figure}[htbp]
\begin{center}
\begin{circuitikz} \draw
(0,0) to[european voltage source, v=U] (0,4) -- (4,4)
  to[L,l=L,i=i] (4,2)
  to[R,l=R] (4,0) -- (0,0)
;
\end{circuitikz}
\caption[RL Circuit]{RL Circuit Diagram}
\label{fig:RL}
\end{center}
\end{figure}

The governing equation of an RL Series Circuit is 
\begin{align}
\frac{\ud}{\ud t} i &= \frac{U - R i}{L} \\
\frac{\ud^2}{\ud t^2} i &= -\frac{R}{L} \frac{\ud}{\ud t} i
\end{align}
%which can be combined to form
%\begin{align}
%-\frac{L}{R} \frac{\ud^2}{\ud t^2} i &= \frac{U - R i}{L}
%\end{align}
%and simplified to
%\begin{align}
%-\frac{L^2}{R^2} \frac{\ud^2}{\ud t^2} i &= \frac{U}{R} - i\\
%L^2 \frac{\ud^2}{\ud t^2} i &= iR^2 - UR
%\end{align}

\subsubsection{Time Domain}

\begin{align}
i R&= U \left( 1 - e^{-t\frac{R}{L}} \right)
\end{align}

\begin{align}
i &= \frac{U}{R} \left( 1 - e^{-t\frac{R}{L}} \right) \\
\frac{\ud}{\ud t} \imath &= \frac{U}{L} e^{-t\frac{R}{L}} \\
\frac{\ud^2}{\ud t^2} \imath &= -\frac{UR}{L^2} e^{-t\frac{R}{L}}
\end{align}

Logarithmic linear regression of first/second derivative?
\begin{align}
\log \left(\frac{L}{U} \frac{\ud}{\ud t} \imath \right) &= -t\frac{R}{L} \\
\log \left( L \right) - \log \left(U \right) + \log \left(\frac{\ud}{\ud t} \imath \right) &= -t\frac{R}{L} \\
\frac{\ud^2}{\ud t^2} \imath &= -\frac{UR}{L^2} e^{-t\frac{R}{L}}
\end{align}

\subsubsection{Combining for L}

Rearranging both equations to be able to drop $R$
\begin{align}
\frac{R}{L} &= \frac{\frac{U}{L} - \dot{\imath}}{\imath} \\
\frac{R}{L} &= - \frac{ \ddot{\imath}}{ \dot{\imath}}
\end{align}
and combining
\begin{align}
\frac{\frac{U}{L} -  \dot{\imath}}{\imath} &= - \frac{\ddot{\imath}}{ \dot{\imath}} \\
\frac{U}{L} -  \dot{\imath} &= - \frac{\ddot{\imath}}{\dot{\imath}} \imath \\
\frac{U}{L}  \dot{\imath} - \dot{\imath}^2 &= - \ddot{\imath} \imath \\
\frac{U}{L}  \dot{\imath} &= \dot{\imath}^2 - \ddot{\imath} \imath \\
L &= U \frac{ \dot{\imath}}{ \dot{\imath}^2 - \ddot{\imath} \imath}
\end{align}

\subsubsection{Combining for R}
\begin{align}
- R \frac{\dot{\imath}}{\ddot{\imath}} &= U \frac{ \dot{\imath}}{ \dot{\imath}^2 - \ddot{\imath} \imath} \\
- R &= U \frac{ \ddot{\imath}}{ \dot{\imath}^2 - \ddot{\imath} \imath}
\end{align}

\subsubsection{Time Constant}

The above formulas for $R$ and $L$ show that the only difference is the appearance of the first vs. second differential of the current in the nominator. As the current curve is an exponential function, both differentials have the same shape, but differ in magnitude by $\tau=L/R$, and thus 
\begin{align}
\tau &= - \frac{\dot{\imath}}{\ddot{\imath}}
\end{align}

\subsection{R Estimation}

The resistance of the circuit can be easily estimated by applying some low PWM duty cycle long enough to reach steady state, and measuring the current.
\begin{align}
R &= D\frac{U}{\imath}
\end{align}

\subsection{L Estimation with a Known R}

Reformulating
\begin{align}
\frac{\ud}{\ud t} i &= \frac{U - R i}{L}
\end{align}
into
\begin{align}
L &= \frac{U - R i}{\frac{\ud}{\ud t} i}
\end{align}
allows inductance estimation with a relatively simple formula.

\subsection{Impedance Estimation}

Exciting a motor coil with a sinusoidal voltage, and measuring the resulting current phase difference and amplitude, the impedance and thus inductance can be calculated. Assuming a pure sinusoidal signal without harmonics,
\begin{gather}
\begin{aligned}
|Z| &= \frac{U_{\textrm{RMS}}}{i_{\textrm{RMS}}} \\
Z &= R + j X \\
Z &= |Z| \left(\cos \theta + j \sin \theta \right)
\end{aligned}
\end{gather}

\subsubsection{Inductance from Impedance}

\begin{gather}
\begin{aligned}
X &= \sqrt{|Z|^2 - R^2} \\
X_L &= \omega L
\end{aligned}
\end{gather}

It looks like this method yields more accurate results than anything looking at $\frac{\ud}{\ud t} i$. This is not surprising: noise and offsets can be removed more effectively as $L$ is computed from averaged current readings, vs.\ being computed from each individual current reading and then averaged.

This method still seems to over-estimate inductance, but seems to get significantly closer. Interestingly, for a 2-phase motor, the estimated impedance running through both phases gets closer to the specified values than both individual phase measurements.

\subsubsection{Phase Estimation}

The phase angle $\theta$ between $U=U_{\textrm{peak}}\sin \omega$ and $i=i_{\textrm{peak}}\sin \left(\omega+\theta\right)$ can be found as the DC component of the composite signal $U(\omega) \times i(\omega)$:
\begin{gather}
\begin{aligned}
U(\omega) \times i(\omega) &= \frac{\cos \theta - \cos\left(2\omega+\theta\right)}{2} \\
\overline{U \times i} &= \frac{1}{2\pi}\int_0^{2\pi} U \times i \ud \omega = U_{\textrm{peak}} i_{\textrm{peak}}\frac{\cos \theta}{2} \\
\cos \theta &= 2 \frac{\overline{U \times i}}{U_{\textrm{peak}} i_{\textrm{peak}}} =\frac{\overline{U \times i}}{U_{\textrm{RMS}} i_{\textrm{RMS}}}
\end{aligned}
\end{gather}

\subsubsection{Resistance from Impedance and Phase}

\begin{gather}
\begin{aligned}
R &= |Z| \cos \theta = \frac{\overline{U i}}{i_{\textrm{RMS}}^2}
\end{aligned}
\end{gather}

As resistance depends on $R \approx \cos \theta$, it is very sensitive to phase shifts, and thus not very reliable for estimation

\subsection{Simultaneous LR Estimation}

Sampling a  applied voltage $U$ step function at fixed intervals $T$, for samples $i_0, i_1, \ldots, i_n$ with t $t>0,n=t/T$, we can compute the differentiations in different ways.

\subsubsection{N3 Sampling}

Assuming linearity around $n=1$:
\begin{align}
{\imath} &= \frac{1}{3} (\imath_0 + \imath_1 + \imath_2) \\
\dot{\imath} &= \frac{1}{2T} (\imath_2 - \imath_0) \\
\ddot{\imath} &= \frac{1}{T^2} (\imath_2 - 2\imath_1 + \imath_0)
\end{align}
and
\begin{align}
L &= U \frac{\dot{\imath}}{\dot{\imath}^2 - \ddot{\imath} \imath}
\end{align}

\section{Single Phase Analysis}

\subsection{Motor Phase Model}

\begin{figure}[htbp]
\begin{center}
\begin{subfigure}[t]{0.45\textwidth}
\begin{tikzpicture}[>=latex]
    % flux axis
    \draw[-,dashed] (0,2) -- (0,-2);
  	\draw[->] (-3,0) -- (3,0) node[anchor=west] {$\mathbf{\mu}$};
	% out winding
    \filldraw[fill=white,thick] (0,2) circle (0.2);
    \fill (0,2) circle (0.0667);
    % in winding
    \filldraw[fill=white,thick] (0,-2) circle (0.2);
    \draw (0.1,-2.1) -- ++(-0.2, 0.2);
    \draw (-0.1,-2.1) -- ++(0.2, 0.2);
	% magnet
	\begin{scope}[rotate=30]
    	\draw[-,dashdotted] (-3,0) -- (3,0);
  		\fill[fill=white] (-1,-0.5) rectangle ++(2,1);
  		\fill[fill=gray] (-1,-0.5) rectangle ++(1,1);
  		\draw[-,thick] (-1,-0.5) rectangle ++(2,1);
   		\draw[] (-0.5,0) node[rotate=30,text=white]{S};
   		\draw[] (0.5,0) node[rotate=30]{N};
   		\fill (0,0) circle (0.0667);
	\end{scope}
	% rotation
    \draw[->]  (0:1.6)  node[anchor=315]{$\theta$} arc (0:30:1.6);

\end{tikzpicture}
\caption{single phase winding and rotor magnet}
\end{subfigure}
\hspace*{\fill}
\begin{subfigure}[t]{0.45\textwidth}
\begin{tikzpicture}[>=latex]
    % flux axis
    \draw[-,dashed] (0,2) -- (0,-2);
   	\draw[->] (-3,0) -- (3,0);
	% out winding
    \filldraw[fill=white,thick] (0,2) circle (0.2);
    \fill (0,2) circle (0.0667);
%    \filldraw[fill=lightgray,thick] (-2,0) circle (0.2);
%    \fill (-2,0) circle (0.0667);
    % in winding
    \filldraw[fill=white,thick] (0,-2) circle (0.2);
    \draw (0.1,-2.1) -- ++(-0.2, 0.2);
    \draw (-0.1,-2.1) -- ++(0.2, 0.2);
%    \filldraw[fill=lightgray,thick] (2,0) circle (0.2);
%    \draw (2.1,-0.1) -- ++(-0.2, 0.2);
%    \draw (1.9,-0.1) -- ++(0.2, 0.2);
	% magnet
	\begin{scope}[rotate=30]
  		\fill[fill=white] (-1,-0.5) rectangle ++(2,1);
  		\fill[fill=gray] (-1,-0.5) rectangle ++(1,1);
  		\draw[-,thick] (-1,-0.5) rectangle ++(2,1);
%   		\draw[] (-0.5,0) node[rotate=30,text=white]{S};
%   		\draw[] (0.5,0) node[rotate=30]{N};
    	\draw[-,dashdotted] (-3,0) -- (0,0);
   		\draw[->, very thick] (0,0) -- (2.5,0) node[anchor=210]{d};
   		\draw[->, very thick] (0,0) -- (0,2.5) node[anchor=300]{q};
   		\draw[-] (0,0.2) -- (0.2,0.2) -- (0.2,0);
   		\fill (0,0) circle (0.0667);
	\end{scope}
	% rotation
    \draw[->]  (0:1.6)  node[anchor=315]{$\theta$} arc (0:30:1.6);

\end{tikzpicture}
\caption{QD coordinates}
\end{subfigure}

\caption[Motor Phase Model]{Single phase winding model. The rotor magnet is at angle $\theta$ relative to the winding's principal field axis $\mu$. The QD coordinate system is aligned with the rotor's magnetic field, instead of the winding's. The \em direct \em component is aligned with the rotor magnet poles, and the \em quadrature \em component is perpendicular to them, electrically.}
\label{fig:singlephaseqd}
\end{center}
\end{figure}

\begin{figure}[htbp]
\begin{center}
\begin{tikzpicture}[>=latex]
    % flux axis
    \draw[-,dashed] (0,2) -- (0,-2);
   	\draw[->] (-3,0) -- (3,0); % node[anchor=south west] {$\mathbf{\mu}$};
	% out winding
    \filldraw[fill=white,thick] (0,2) circle (0.2);
    \fill (0,2) circle (0.0667);
    % in winding
    \filldraw[fill=white,thick] (0,-2) circle (0.2);
    \draw (0.1,-2.1) -- ++(-0.2, 0.2);
    \draw (-0.1,-2.1) -- ++(0.2, 0.2);
	% magnet
	\begin{scope}[rotate=30]
   		\draw[->,very thick] (0,0) -- (2.5,0) node[anchor=210]{$I_d$};
   		\draw[->,very thick] (0,0) -- (0,2.5) node[anchor=300]{$I_q$};
   		\draw[-] (0,0.2) -- (0.2,0.2) -- (0.2,0);
	\end{scope}
	% rotation
    \draw[->]  (0:1.6)  node[anchor=315]{$\theta$} arc (0:30:1.6);
    % projections
  
    \fill (0,0) circle (0.0667);
    \draw[-,dotted] (120:2.5) -- ( {-2.5*sin(30)}, 0 );
    \draw[->,very thick] (0,0) -- ( {-2.5*sin(30)}, 0 ) node[sloped,below] {$i_q = -I_q \sin \theta$};
    \draw[-,dotted] (30:2.5) -- ( {2.5*cos(30)}, 0 );
    \draw[->,very thick] (0,0) -- ( {2.5*cos(30)}, 0 ) node[sloped,below] {$i_d = I_d \cos \theta$};

\end{tikzpicture}

\caption[QD to Phase Projection]{Projection of the QD coordinate system currents onto the principal axis of a single winding.}
\label{fig:qdproj}
\end{center}
\end{figure}

\begin{figure}[htbp]
\begin{center}
\begin{circuitikz}[]
\draw (0,5) node[anchor=180]{$U$}
  to[V,v<=$E$,i=$i$,o-*] ++(0,-2) node[anchor=180]{$U'$}
  to[L=$L$] ++(0,-1.5)
  to[R=$R$,-] ++(0,-1.5) node[rground]{}
;
\end{circuitikz}
\caption[Single Phase Model]{Single phase motor winding model that is composed of a passive LR part, and the BEMF component $E$.}
\label{fig:singlephase}
\end{center}
\end{figure}

\begin{figure}[htbp]
\begin{center}
\begin{tikzpicture}[>=latex]
%    \draw (0,0) circle (3);
   	\draw[->,dotted] (-3,0) -- (3,0); % node[anchor=west] {re};
   	\draw[->,dotted] (0,-3) -- (0,3); % node[anchor=south] {im};
   	\draw[->] (0,0) -- (30:3) node[anchor=210] {d};
   	\draw[->] (0,0) -- (120:3) node[anchor=300] {q};
    \draw[->]  (0:2.7)  node[anchor=315]{$\theta$} arc (0:30:2.7);
%    \draw[->, thick,dashed]  (0,0) -- (30:2.5) node[anchor=300] {$E$};
%    \draw[->, thick,dashed]  (0,0) -- (120:2.5) node[anchor=210] {$\tau$};
%    \draw[->, very thick]  
%        (30:0.5) coordinate (D)
%        (120:1.5) coordinate (Q)
%    	(0,0) -- (D) node[anchor=300] {$i_d$}
%    	(0,0) -- (Q) node[anchor=210] {$i_q$}
%    	(0,0) -- ($(D) + (Q)$) node[anchor=south] {$i$}
%	;
    \draw[->, very thick]  (0,0) -- (30:0.75) node[anchor=south] {$I_d$};
    \draw[->, very thick]  (0,0) -- (120:2) node[anchor=0] {$I_q$};
    \draw[->, very thick]  (0,0) -- ($(30:0.75) + (120:2)$) node[anchor=south] {$I$};
    \draw[-, dotted]  (30:0.75) -- ($(30:0.75) + (120:2)$) -- (120:2);

\end{tikzpicture}
\caption[Phasors]{Current phasor for a rotating stator field and PM rotor in a QD coordinate system.}
%\label{fig:singlephase}
\end{center}
\end{figure}

The single phase winding electrical model
\begin{gather}
\begin{aligned}
\label{eq:singlephase} 
U &= E + R \imath + L \frac{\partial \imath}{\partial t}
\end{aligned}
\end{gather}
as depicted in \cref{fig:singlephase}, with a sinusoidal BEMF voltage
\begin{gather}
\begin{aligned}
\label{eq:sineemf} 
E_k &= k_e \omega_m \cos \left( n \theta_m + \phi_{0} \right) = k_e \omega_m \cos \left( \theta_{e} + \phi_0 \right)
\end{aligned}
\end{gather}
is the starting point for modeling motor windings for control purposes.

The BEMF component $E$ is only dependent on rotor position and speed, while the impedance component $L \frac{\partial \imath}{\partial t} + R\imath$ is only dependent the current. Under constant-speed and torque conditions, both are in sync with a speed and torque dependent phase shift.

Assuming a sinusoidal magnetic characteristic, the torque contribution from each phase is
\begin{gather}
\begin{aligned}
\tau &= - k \sin \left( \theta_e + \phi_{0}\right) \cdot \imath.
\end{aligned}
\end{gather}

The phase current $\imath$ can be decomposed, as shown in \cref{fig:qdproj}, into a \em direct \em component that is synchronously in-phase with the rotor magnet
\begin{gather}
\begin{aligned}
\imath_d &= I_d \cos \left( \theta_e + \phi_{0}\right) = I_d \cos \left( \theta \right),
\end{aligned}
\end{gather}
and an orthogonal \em quadrature \em component that is in-phase with the torque producing component of the magnetic field
\begin{gather}
\begin{aligned}
\imath_q &= - I_q \sin \left( \theta_e + \phi_{0}\right) = - I_q \sin \left( \theta \right).
\end{aligned}
\end{gather}
The quadrature component $\imath_q$ is strictly contributing to torque, while $\imath_d$ has a net zero effect, and the total current magnitude is described by
\begin{gather}
\begin{aligned}
I^2 &= I_d^2 + I_q^2.
\end{aligned}
\end{gather}

\subsection{Field Oriented Control}

\em Field Oriented Control \em adjusts the winding voltage's phase angle to keep the current phase locked to the motor angle, extracting maximum torque for a given motor current, regardless of motor speed. However, when shifting the current phase, the contributions to the voltage and torque waveforms change, and this can be used for
\begin{itemize}
\item field weakening, to increase top speed at the expense of available torque,
\item and flux braking, to dissipate excess DC bus voltage without changing the output torque.
\end{itemize}

\subsubsection{Full Winding Equation}

The complete motor winding voltage, in terms of QD currents, is thus given by 
\begin{gather}
\begin{aligned}
%\label{eq:singlephase} 
U &= E + R (\imath_d + \imath_q) + L \frac{\partial (\imath_d + \imath_q)}{\partial t} \\
%U &= E + R I_d \cos \left( \theta \right) - R I_q \sin \left( \theta \right) \\
%&\quad - L \omega_e I_d \sin \left( \theta \right) - L \omega_e I_q \cos \left( \theta \right) \\
%&\quad + L \frac{\partial I_d}{\partial t} \cos \left(\theta \right) - L \frac{\partial I_q}{\partial t} \sin \left(\theta \right) \\
&= - ( R I_q + L \omega_e I_d + L \frac{\partial I_q}{\partial t})\sin \left( \theta \right) \\
&\quad + ( k_e \omega_e + R I_d - L \omega_e I_q + L \frac{\partial I_d}{\partial t}) \cos \left( \theta \right)
\end{aligned}
\end{gather}
Thus, the direct and quadrature components of $U$ are   
\begin{gather}
\begin{aligned}
%\label{eq:singlephase} 
U_q &= R I_q + L \omega_e I_d + L \frac{\partial I_q}{\partial t} \\
U_d &= k_e \omega_e + R I_d - L \omega_e I_q + L \frac{\partial I_d}{\partial t}
\end{aligned}
\end{gather}
for a magnitude of 
\begin{gather}
\begin{aligned}
%\label{eq:singlephase} 
U^2 &= U_d^2 + U_q^2 \\
	&= ( R I_q + L \omega I_d + L \frac{\partial I_q}{\partial t})^2 + ( k_e \omega + R I_d - L \omega I_q + L \frac{\partial I_d}{\partial t})^2 \\
%	&= R^2 I_q^2 + L^2 \omega^2 I_d^2 + L^2 \left( \frac{\partial I_q}{\partial t} \right)^2 + 2 R I_q L \omega I_d + 2 L \omega I_d L \frac{\partial I_q}{\partial t} + 2 R I_q L \frac{\partial I_q}{\partial t} \\
%	&\quad + k_e^2 \omega^2 + R^2 I_d^2 + L^2 \omega^2 I_q^2 + L^2 \left(\frac{\partial I_d}{\partial t}\right)^2 \\
%	&\quad + 2 k_e \omega R I_d - 2 k_e \omega L \omega I_q + 2 k_e \omega L \frac{\partial I_d}{\partial t} \\
%	&\quad - 2 R I_d L \omega I_q + 2 R I_d L \frac{\partial I_d}{\partial t} - 2 L \omega I_q L \frac{\partial I_d}{\partial t}\\
	&= \left(R^2 + L^2 \omega^2 \right) I^2 + L^2 \left(\frac{\partial I_d}{\partial t}\right)^2 + L^2 \left(\frac{\partial I_q}{\partial t}\right)^2 + k_e^2 \omega^2\\
%	&\quad - R L \omega I_d I_q + R L \omega I_d I_q
	&\quad + 2 R L \left( I_d \frac{\partial I_d}{\partial t} + I_q \frac{\partial I_q}{\partial t} \right) \\
	&\quad + 2 L^2 \omega \left(I_d \frac{\partial I_q}{\partial t} - I_q \frac{\partial I_d}{\partial t} \right) \\ 
	&\quad + 2 k_e \omega \left(R I_d - L \omega I_q + L \frac{\partial I_d}{\partial t} \right).
\end{aligned}
\end{gather}

\subsubsection{Constant Speed Analysis}

Assuming constant speed and current, the equation simplifies to
\begin{gather}
\begin{aligned}
%\label{eq:singlephase} 
U^2 &= \left(R^2 + L^2 \omega^2 \right) I^2 + k_e^2 \omega^2  + 2 k_e \omega \left( R I_d - L \omega I_q \right),
\end{aligned}
\end{gather}
from which we can see that $\left( R I_d - L \omega I_q \right)$ remains to influence the magnitude of $U$ by varying $I_d, I_q$. The ratio of the two can be varied via the phase angle $\alpha$, relative to maximum torque, with $I_d = - I \sin \alpha$ and $I_q = I \cos \alpha$ without changing the current magnitude $I$. Differentiating 
\begin{gather}
\begin{aligned}
%\label{eq:singlephase} 
R I_d - L \omega_e I_q &= I \left( - R \sin \alpha - L \omega \cos \alpha \right)
\end{aligned}
\end{gather}
with respect to $\alpha$ yields
\begin{gather}
\begin{aligned}
%\label{eq:singlephase} 
\frac{\partial}{\partial \alpha} \left(- R \sin \alpha - L \omega \cos \alpha \right) &= - R \cos \alpha + L \omega \sin \alpha,
\end{aligned}
\end{gather}
which shows that as we move away from $\alpha = 0$, the magnitude of the phase voltage $U$ can be decreased. This happens when
\begin{gather}
\begin{aligned}
%\label{eq:singlephase} 
- R \cos \alpha - L \omega \sin \alpha < 0,
\end{aligned}
\end{gather}
and thus when
\begin{gather}
\begin{aligned}
%\label{eq:singlephase} 
- \frac{R}{L \omega} < \tan \alpha,
\end{aligned}
\end{gather}
changing the current phase $\alpha$ will result in reduced phase voltage.

\section{3-Phase Star}

\begin{figure}[htbp]
\begin{center}
\begin{subfigure}[t]{0.45\textwidth}
\begin{tikzpicture}[>=latex]
    % flux axis
    \draw[-,dashed] (0,2.2) node[anchor=270]{A};
    \draw[-,dashed] (210:2.2) node[anchor=30]{C};
    \draw[-,dashed] (330:2.2) node[anchor=150]{B};
    \draw[-,dashed] (0,2) -- (0,-2);
    \draw[-,dashed] (210:2.0) -- (30:2);
    \draw[-,dashed] (330:2.0) -- (150:2.0);
   	\draw[->] (-3,0) -- (3,0);
	% out winding
    \filldraw[fill=white,thick] (0,2) circle (0.2);
    \fill (0,2) circle (0.0667);
    \filldraw[fill=gray,thick] (210:2.0) circle (0.2);
    \fill (210:2.0) circle (0.0667);
    \filldraw[fill=lightgray,thick] (330:2.0) circle (0.2);
    \fill (330:2.0) circle (0.0667);
    % in winding
    \filldraw[fill=white,thick] (0,-2) circle (0.2);
    \draw (0.1,-2.1) -- ++(-0.2, 0.2);
    \draw (-0.1,-2.1) -- ++(0.2, 0.2);
    \filldraw[fill=gray,thick] (30:2.0) circle (0.2);
    \draw ($(30:2.0) + (0.1,-0.1)$) -- ++(-0.2, 0.2);
    \draw ($(30:2.0) + (-0.1,-0.1)$) -- ++(0.2, 0.2);
    \filldraw[fill=lightgray,thick] (150:2.0) circle (0.2);
    \draw ($(150:2.0) + (0.1,-0.1)$) -- ++(-0.2, 0.2);
    \draw ($(150:2.0) + (-0.1,-0.1)$) -- ++(0.2, 0.2);
	% magnet
	\begin{scope}[rotate=30]
%  		\fill[fill=white] (-1,-0.5) rectangle ++(2,1);
%  		\fill[fill=gray] (-1,-0.5) rectangle ++(1,1);
%  		\draw[-,thick] (-1,-0.5) rectangle ++(2,1);
%   		\draw[] (-0.5,0) node[rotate=30,text=white]{S};
%   		\draw[] (0.5,0) node[rotate=30]{N};
%    	\draw[-,dashdotted] (-3,0) -- (0,0);
%   		\draw[->, very thick] (0,0) -- (2.5,0) node[anchor=210]{d};
%   		\draw[->, very thick] (0,0) -- (0,2.5) node[anchor=300]{q};
%   		\draw[-] (0,0.2) -- (0.2,0.2) -- (0.2,0);
   		\fill (0,0) circle (0.0667);
	\end{scope}
	% rotation
    \draw[->]  (0:1.6)  node[anchor=315]{$\theta$} arc (0:20:1.6);
    % phase to phase arrows
    \draw[->,thick]  (87:1.0)  arc (87:-27:1.0);
    \draw[->,thick]  (-33:1.0)  arc (-33:-147:1.0);
    \draw[->,thick]  (-153:1.0)  arc (-153:-267:1.0);

\end{tikzpicture}
\caption{Phases}
\end{subfigure}
\hspace*{\fill}
\begin{subfigure}[t]{0.45\textwidth}
\begin{circuitikz}[
	R/.style={european resistor}
]
\draw (0,3) node[anchor=270]{$U$}
  to[R,l=$A$,f=$i_A$,o-] ++(0,-2)
  to[short] ++(0,-1) node[anchor=210]{$N$}
;
\draw (-2.598,-1.5) node[anchor=30]{$V$}
  to[R,l=$B$,f=$i_B$,o-] ++(1.732, 1.0)
  to[short,] ++(0.866, 0.5)
;
\draw (2.598,-1.5) node[anchor=150]{$W$}
  to[R,l=$C$,f=$i_C$,o-] ++(-1.732, 1.0)
  to[short,-*] ++(-0.866, 0.5)
;

\end{circuitikz}
\caption{Star Connection}
\end{subfigure}

\caption[3-Phase Star]{3-Phase Star / Wye Connection. Phases are arranged clockwise (physically \unit{-120}{\degree}) with a resultant $\phi = \unit{120}{\degree}$ electrical offset.}
\label{fig:star}
\end{center}
\end{figure}

\begin{figure}[htbp]
\begin{center}
\begin{tikzpicture}[>=latex]
	\begin{axis}[
	width=0.667\textwidth,
	height=0.667\textwidth,
	title=3-Phase Wye Voltage Waveforms, xlabel={$\lambda$}, ylabel={$U_{\mathrm{bus}} / U_{\mathrm{winding}}$}, xmin=0, xmax=2*pi, clip=false,
	axis equal=true,
	enlarge x limits=false,
	xmajorgrids,
	ymajorgrids,
	yminorgrids,
	xtick={0,pi/3, 2*pi/3, pi, 4/3*pi, 5/3*pi, 2*pi},
	xticklabels={{$\frac{0}{3}\pi$}, {$\frac{1}{3}\pi$}, {$\frac{2}{3}\pi$}, {$\frac{3}{3}\pi$}, {$\frac{4}{3}\pi$}, {$\frac{5}{3}\pi$}, {$\frac{6}{3}\pi$}},
	ytick={-3, -sqrt(3), -1, 0, 1, sqrt(3), 3},
	yticklabels={{$-3$}, {$-\sqrt{3}$}, {$-1$}, {$0$}, {$1$}, {$\sqrt{3}$}, {$3$}},
	minor ytick={-3,-2,-1,0,1,2,3},
	major y grid style={dashed,very thin},
	major x grid style={very thin},
	minor y grid style={very thin},
	]
	\addplot[domain=0:2*pi,samples=361,red!40!black] {cos(deg(x))} node [pos=1,pin=3:{$A$}] {};
	\addplot[domain=0:2*pi,samples=361,green!0!black] {cos(deg(x)+120)} node [pos=1,pin=-30:{$B$}] {};
	\addplot[domain=0:2*pi,samples=361,blue!0!black] {cos(deg(x)+240)} node [pos=1,pin=30:{$C$}] {};
	\addplot[domain=0:2*pi,samples=361,dashed] {sqrt(3)*cos(deg(x)+150)} node [pos=1/12,pin=-75:{$B - A$}] {};
	\addplot[domain=0:2*pi,samples=361,dashdotted] {sqrt(3)*cos(deg(x)+270)} node [pos=9/12,pin=-75:{$C - B$}] {};
	\addplot[domain=0:2*pi,samples=361,dashdotted] {sqrt(3)*cos(deg(x)+30)} node [pos=5/12,pin=-75:{$A - C$}] {};
	% "saddle" type driving 
%	\addplot[domain=0:2*pi,samples=361,red] {max(0, max(cos(deg(x)) - cos(deg(x)+120), cos(deg(x)) - cos(deg(x)+240)))} node[pos=1/12,pin=30:{$U = \mathrm{max} \left( 0, U_A-U_B, U_A-U_C \right)$}]{};
	% following equation for U_N is not wrong, but it is "asymmetric", creating the "double bump" terminal voltage
%	\addplot[domain=0:2*pi,samples=361,gray] {max(0, max(cos(deg(x)) - cos(deg(x)+120), cos(deg(x)) - cos(deg(x)+240))) - cos(deg(x))} node [pos=1,pin=0:{$U_N$}] {};
	% following is the symmetrical approximation equation for U_N
%	\addplot[domain=0:2*pi,samples=361,gray] {sqrt(3)/2 + (1-sqrt(3)/2)*cos(deg(3*x)+180)} node [pos=1,pin=-3:{$U_N$}]{};
	\addplot[domain=0:2*pi,samples=361,red] {
		cos(deg(x)) 
		+ mod(int(x/(pi/3)+0.5),2)*max(max(abs(cos(deg(x)+0)),abs(cos(deg(x)+120))),abs(cos(deg(x)+240)))
		+ (1 - mod(int(x/(pi/3)+0.5),2))*(sqrt(3) - max(max(abs(cos(deg(x)+0)),abs(cos(deg(x)+120))),abs(cos(deg(x)+240))))
%		+ sqrt(3)/2 + (1-sqrt(3)/2)*cos(deg(3*x)+180)
	} node[pos=1/12,pin=45:{$U = N + A$}]{};
	\addplot[domain=0:2*pi,samples=361,green] {
		cos(deg(x)+120) 
		+ mod(int(x/(pi/3)+0.5),2)*max(max(abs(cos(deg(x)+0)),abs(cos(deg(x)+120))),abs(cos(deg(x)+240)))
		+ (1 - mod(int(x/(pi/3)+0.5),2))*(sqrt(3) - max(max(abs(cos(deg(x)+0)),abs(cos(deg(x)+120))),abs(cos(deg(x)+240))))
%		+ sqrt(3)/2 + (1-sqrt(3)/2)*cos(deg(3*x)+180)
	};
	\addplot[domain=0:2*pi,samples=361,blue] {
		cos(deg(x)+240) 
		+ mod(int(x/(pi/3)+0.5),2)*max(max(abs(cos(deg(x)+0)),abs(cos(deg(x)+120))),abs(cos(deg(x)+240)))
		+ (1 - mod(int(x/(pi/3)+0.5),2))*(sqrt(3) - max(max(abs(cos(deg(x)+0)),abs(cos(deg(x)+120))),abs(cos(deg(x)+240))))
%		+ sqrt(3)/2 + (1-sqrt(3)/2)*cos(deg(3*x)+180)
	};
	% experimental
%	\addplot[domain=0:2*pi,samples=361,red] {max(0, sqrt(3)*cos(deg(x)+270) - min(sqrt(3)*cos(deg(x)+30), sqrt(3)*cos(deg(x)+150)))};
%	\addplot[domain=0:2*pi,samples=361,red] {max(0, sqrt(3)*cos(deg(x)+30) - min(sqrt(3)*cos(deg(x)+150), sqrt(3)*cos(deg(x)+270)))};
%	\addplot[domain=0:2*pi,samples=201,dotted] {cos(deg(x)+240)-cos(deg(x)+120)} node [pos=1/2,pin=30:{$U_{BC}$}] {};
%	\addplot[domain=0:2*pi,samples=201,dotted] {cos(deg(x))-cos(deg(x)+240)} node [pos=2/3,pin=-30:{$U_{CA}$}] {};
%	\addplot[domain=0:2*pi,samples=201,thick] { % U = 
%		sin(deg(x)+120)-sin(deg(x)) % V - U_UV 
%		 - min(sin(deg(x)+240)-sin(deg(x)+120),sin(deg(x))-sin(deg(x)+240)) + sqrt(3)*4/3} node [pos=1/3,pin=-30:{$U_{V}$}] {};

%	\addplot[domain=0:2*pi,samples=361,cyan,thick,dashed] {sqrt(3)/2 - 0.5*cos(deg(x))*cos(deg(x)+120)*cos(deg(x)+240)};
	% plots with proper U_N voltage segments for U/A
	% U_N for (4n-1)/6pi <= x < (4n+1)/6pi is sqrt(3)-max(abs(U_A), abs(U_B), abs(U_C))
	% U_N for (4n+1)/6pi <= x < (4n+3)/6pi is max(abs(U_A), abs(U_B), abs(U_C))
	\addplot[domain=0/3*pi:6/3*pi,samples=361,gray] {
		mod(int(x/(pi/3)+0.5),2)*max(max(abs(cos(deg(x)+0)),abs(cos(deg(x)+120))),abs(cos(deg(x)+240)))
		+ (1 - mod(int(x/(pi/3)+0.5),2))*(sqrt(3) - max(max(abs(cos(deg(x)+0)),abs(cos(deg(x)+120))),abs(cos(deg(x)+240))))
	} node [pos=1,pin=0:{$N$}]{};
%	\addplot[domain=0/3*pi:6/3*pi,samples=61,cyan,thick] {mod(int(x/(pi/3)+0.5),2)};
	% drawn by segment
%	\addplot[domain=0/3*pi:0.5/3*pi,samples=61,cyan,thick,dashed] {sqrt(3)+cos(deg(x)+180)};
%	\addplot[domain=0/3*pi:0.5/3*pi,samples=61,cyan,dashed] {cos(deg(x))+sqrt(3)+cos(deg(x)+180)};
%	\addplot[domain=0.5/3*pi:1.5/3*pi,samples=61,cyan,thick,dashed] {cos(deg(x)-60)};
%	\addplot[domain=0.5/3*pi:1.5/3*pi,samples=61,cyan,dashed] {cos(deg(x))+cos(deg(x)-60)};
%	\addplot[domain=2.5/3*pi:3.5/3*pi,samples=61,cyan,thick,dashed] {cos(deg(x)+180)};
%	\addplot[domain=2.5/3*pi:3.5/3*pi,samples=61,cyan,dashed] {cos(deg(x))+cos(deg(x)+180)};
\end{axis}
\end{tikzpicture}

\caption[Star Waveforms]{3-phase star connection winding and terminal voltage waveforms, showing how terminal voltage is derived from the individual winding and inter-phase voltages.}
\label{fig:waveform3}
\end{center}
\end{figure}

In 3 phase star / Wye configuration, the three motor windings $A,B,C$ are connected to three terminals $U,V,W$ with their other ends tied together at a common node $N$. Each of $U,V,W$ is connected to a half-bridge.

\begin{gather}
\begin{aligned}
\frac{\ud i_A}{\ud t} &= \frac{2 U' - V' - W' - 3 R i_A}{3 L} \\
\frac{\ud i_B}{\ud t} &= \frac{2 V' - W' - U' - 3 R i_B}{3 L} \\
\frac{\ud i_C}{\ud t} &= \frac{2 W' - U' - V' - 3 R i_C}{3 L}
\end{aligned}
\end{gather}

\subsection{3-Phase Phasors}

Each phase voltage $A,B,C$ is a simple sinusoid of the form $\cos \left( \lambda + \phi \right)$. As any linear combination of sinusoids is just another sinusoid, the voltages $V-U$, $W-V$, $U-W$ between the bridge terminals are also simple sinusoids. 

For a 3-phase system, the phases are offset by $\phi = \unit{120}{\degree}$ from each other.
\begin{gather}
\begin{aligned}
A &= \cos \left( \lambda  + \unit{0}{\degree}\right) \\
B &= \cos \left( \lambda + \unit{120}{\degree} \right)\\
C &= \cos \left( \lambda + \unit{240}{\degree} \right) \\
% cos x - cos (x+120) = a cos (x + b)
% a -> [cos^2 + sin^2] -> a^2 = (1+0.5)^2 + (0 - sqrt(3)/2)^2 = 9/4 + 3/4 = 3
% b -> [atan(sin/cos)] -> atan( (-sqrt(3) / 2) / 1.5 ) = 330deg
V-U &= B - A = \cos \left( \lambda + \unit{120}{\degree} \right) - \cos \left( \lambda \right) = \sqrt(3) \cos  \left( \lambda  + \unit{150}{\degree} \right)\\
W-V &= C - B = \sqrt(3) \cos  \left( \lambda  + \unit{270}{\degree} \right)\\
U-W &= A - C = \sqrt(3) \cos  \left( \lambda  + \unit{30}{\degree} \right)\\
\end{aligned}
\end{gather}

The terminal voltages $U,V,W$ have to be such that the relative voltages always satisfy the above relations without exceeding the available bus voltage.

\Cref{fig:waveform3} shows the 3-phase waveform diagram. By choosing $U_N$ right, one can maximize the $U_{\mathrm{bus}}/U_{\mathrm{winding}}$ ratio. As the diagram shows, this can be achieved by compensating for the peaks of the phase sinusoids with
\begin{gather}
\begin{aligned}
N &= \begin{cases}
 \frac{\sqrt{3}}{2} - \left( -\frac{\sqrt{3}}{2} + \mathrm{max} (A, B, C) \right) & if $\frac{4n+1}{12\pi} \leq \lambda < \frac{4n+3}{12\pi}$ \\
 \frac{\sqrt{3}}{2} - \left( \frac{\sqrt{3}}{2} + \mathrm{min} (A, B, C) \right) & if $\frac{4n-1}{12\pi} \leq \lambda < \frac{4n+1}{12\pi}$    
\end{cases},
\end{aligned}
\end{gather}
resulting in a winding voltage that is only a factor of $\sqrt{3}$ lower than the bus voltage\footnote{A close approximation is $U_N = \sqrt{3}/2 - (1-\sqrt{3}/2) \cos 3\lambda$, but this results in slight overswing of the terminal voltages.}.

\section[2Ph Mot w/ 3Ph Driver]{2-Phase Motor With 3-Phase Driver}

\begin{figure}[htbp]
\begin{center}
\begin{subfigure}[t]{0.45\textwidth}
\begin{tikzpicture}[>=latex]
    % flux axis
    \draw[-,dashed] (0,2.2) node[anchor=270]{A};
    \draw[-,dashed] (0:2.2) node[anchor=225]{B};
    \draw[-,dashed] (0,2) -- (0,-2);
    \draw[-,dashed] (0:2.0) -- (180:2.0);
   	\draw[->] (2,0) -- (3,0);
	% out winding
    \filldraw[fill=white,thick] (0,2) circle (0.2);
    \fill (0,2) circle (0.0667);
    \filldraw[fill=lightgray,thick] (0:2.0) circle (0.2);
    \fill (0:2.0) circle (0.0667);
    % in winding
    \filldraw[fill=white,thick] (0,-2) circle (0.2);
    \draw (0.1,-2.1) -- ++(-0.2, 0.2);
    \draw (-0.1,-2.1) -- ++(0.2, 0.2);
    \filldraw[fill=lightgray,thick] (180:2.0) circle (0.2);
    \draw ($(180:2.0) + (0.1,-0.1)$) -- ++(-0.2, 0.2);
    \draw ($(180:2.0) + (-0.1,-0.1)$) -- ++(0.2, 0.2);
	% magnet
	\begin{scope}[rotate=30]
%  		\fill[fill=white] (-1,-0.5) rectangle ++(2,1);
%  		\fill[fill=gray] (-1,-0.5) rectangle ++(1,1);
%  		\draw[-,thick] (-1,-0.5) rectangle ++(2,1);
%   		\draw[] (-0.5,0) node[rotate=30,text=white]{S};
%   		\draw[] (0.5,0) node[rotate=30]{N};
%    	\draw[-,dashdotted] (-3,0) -- (0,0);
%   		\draw[->, very thick] (0,0) -- (2.5,0) node[anchor=210]{d};
%   		\draw[->, very thick] (0,0) -- (0,2.5) node[anchor=300]{q};
%   		\draw[-] (0,0.2) -- (0.2,0.2) -- (0.2,0);
   		\fill (0,0) circle (0.0667);
	\end{scope}
	% rotation
    \draw[->]  (0:1.6)  node[anchor=315]{$\theta$} arc (0:20:1.6);
    % phase to phase arrows
    \draw[->,thick]  (87:1.0)  arc (87:3:1.0);

\end{tikzpicture}
\caption{Phases}
\end{subfigure}
\hspace*{\fill}
\begin{subfigure}[t]{0.45\textwidth}
\begin{circuitikz}[R/.style={european resistor}]
\draw (-3,0) node[anchor=270]{U}
  to[R,l=$A$,f=$i_A$,o-] ++(2,0)
  to[short] ++(1,0) node[anchor=270]{V}
;
\draw (3,0) node[anchor=270]{W}
  to[R,l=$B$,f=$i_B$,o-] ++(-2,0)
  to[short,-o] ++(-1,0)
;

\end{circuitikz}
\caption{2/3 Connection}
\end{subfigure}

\caption[2-Phase w/ 3 Terminals]{2 Phases connected to 3 terminals. Phases are arranged clockwise (physically \unit{-90}{\degree}) with a resultant $\phi = \unit{90}{\degree}$ electrical offset. Unlike a 3-phase system, it is not rotationally symmetrical.}
\label{fig:2ph3ph}
\end{center}
\end{figure}

\begin{figure}[htbp]
\begin{center}
\begin{tikzpicture}[>=latex]
\begin{axis}[
	width=0.667\textwidth,
	height=0.667\textwidth,
	title=2-Phase 3-Terminal Voltage Waveforms, xlabel={$\lambda$}, ylabel={$U / U_{\mathrm{winding}}$}, xmin=0, xmax=2*pi, clip=false,
	axis equal=true,
	enlarge x limits=false,
	xmajorgrids,
	ymajorgrids,
	yminorgrids,
	xtick={0,pi/2, pi, 3/2*pi, 2*pi},
	xticklabels={{$0$}, {$\frac{1}{2}\pi$}, {$\pi$}, {$\frac{3}{2}\pi$}, {$2\pi$}},
	ytick={-sqrt(2), -1, 0, 1, sqrt(2)},
	yticklabels={{$-\sqrt{2}$}, {$-1$}, {$0$}, {$1$}, {$\sqrt{2}$}},
	minor ytick={-2,2},
	major y grid style={dashed},
	]
	\addplot[domain=0:2*pi,samples=361] {cos(deg(x))} node [pos=1,pin=0:{$A$}] {};
	\addplot[domain=0:2*pi,samples=361] {cos(deg(x)+90)} node [pos=1,pin=-60:{$B$}] {};
%	\addplot[domain=0:2*pi,samples=361,dashed] {sqrt(2)*cos(deg(x)+135)} node [pos=1.25/12,pin=-90:{$U_B - U_A$}] {};
	\addplot[domain=0:2*pi,samples=361,dashed] {cos(deg(x)+90) - cos(deg(x)+0)} node [pos=1.25/12,pin=-15:{$B - A$}] {};
	\addplot[domain=0:2*pi,samples=361,dashdotted] {cos(deg(x)+0) - cos(deg(x)+90)} node [pos=7.25/12,pin=-15:{$A - B$}] {};
	% terminal voltage for U
	\addplot[domain=0:2*pi,samples=361,red] {sqrt(2)/2 + 0.5*(cos(deg(x)+0) - cos(deg(x)+90))} node[pos=1,pin=30:{$U = V + A$}]{};
	\addplot[domain=0:2*pi,samples=361,blue] {sqrt(2)/2 + 0.5*(cos(deg(x)+90) - cos(deg(x)+0))} node[pos=1,pin=-30:{$W = V + B$}]{};
	\addplot[domain=0:2*pi,samples=361,green] {sqrt(2)/2 + sqrt(2)/2*(cos(deg(x)-135))} node[pos=1,pin=5:{$V=\frac{ \sqrt{2} - (A + B)}{2}$}]{};
%	\addplot[domain=0:2*pi,samples=361,cyan,dashed] {0.5 * (sqrt(2) - cos(deg(x)+0) - cos(deg(x)+90))};
%	\addplot[domain=0:2*pi,samples=361,cyan,dashed] {sqrt(2)/2 + sqrt(2)/2*(cos(deg(x)-135)) + cos(deg(x)) }; % U via addition of V+U_A
\end{axis}
\end{tikzpicture}

\caption[2/3 Waveforms]{2-phase 3-terminal connection winding and terminal voltage waveforms, showing how terminal voltages are derived from the individual winding and inter-phase voltages.}
\label{fig:waveform23}
\end{center}
\end{figure}

In theory, all motor parameters can be estimated by sequentially turning one half bridge low, while the others are switched high, allowing current to simultaneously flow in at two places, but only out at one. However, the parameter estimation is difficult with noisy values.

\subsection{Full Dynamic Circuit}

\begin{figure}[htbp]
\begin{center}
\begin{circuitikz} 
\draw (0,8) 
  to[R,] ++(0,-2)
  to[normal open switch,] ++(0,-1)
  to[R,] ++(0,-2)
  to[R,] ++(0,-2)
  to[normal open switch,l=$A$] ++(0,-1)
;
\draw (4,8) node[vcc]{U}
  to[R,] ++(0,-2)
  to[normal open switch,] ++(0,-1)
  to[R,] ++(0,-2)
  to[R,] ++(0,-2)
  to[normal open switch,l=$B$] ++(0,-1)
  node[rground]{}
;
\draw (8,8) 
  to[R,l=$R_T$] ++(0,-2)
  to[normal open switch,] ++(0,-1)
  to[R,l=$R_T$] ++(0,-2)
  to[R,l=$R_S$] ++(0,-2)
  to[normal open switch,l=$C$] ++(0,-1)
;
\draw (0,0)
  to[short,-*] ++(4,0)
  to[short] ++(4,0)
;
\draw (0,5)
  to[R,l=$R_P$,*-] ++(2,0)
  to[L,l=$L_P$,] ++(2,0)
  to[R,*-] ++(2,0)
  to[L,-*] ++(2,0)
;
\draw (0,8)
  to[short,-*] ++(4,0)
  to[short] ++(4,0)
;

\end{circuitikz}
\caption[ABBC Driver]{3-Phase Driver with 2-Phase Motor with phase resistance $R_P$ and switching resistance $R_T$ and shunt resistance $R_S$.}
\label{fig:ABBC}
\end{center}
\end{figure}

\begin{figure}[htbp]
\begin{center}
\begin{circuitikz} 
\draw (0,8) 
  to[R,] ++(0,-2)
  to[normal open switch,] ++(0,-1)
  to[R] ++(0,-2)
  to[R,f=$i_A$] ++(0,-2)
  to[short,l=$A$] ++(0,-1)
;
\draw (4,8) node[vcc]{U}
  to[R,f=$i_b$] ++(0,-2)
  to[short,] ++(0,-1)
  to[R,] ++(0,-2)
  to[R,] ++(0,-2)
  to[normal open switch,l=$B$] ++(0,-1)
  node[rground]{}
;
\draw (8,8) 
  to[R,l=$R_T$,f=$i_c$] ++(0,-2)
  to[short,] ++(0,-1)
  to[R,l=$R_T$,] ++(0,-2)
  to[R,l=$R_S$,] ++(0,-2)
  to[normal open switch,l=$C$] ++(0,-1)
;
\draw (0,0)
  to[short,-*] ++(4,0)
  to[short] ++(4,0)
;
\draw (0,5) node[circ,label={[shift={(-0.4,0.0)}]:{$U_a$}}]{}
  to[R,l_=$R_P$,*-] ++(2,0)
  to[L,l_=$L_P$,] ++(2,0) node[circ,label={[shift={(-0.3,0.0)}]:{$U_b$}}]{}
  to[R,-] ++(2,0)
  to[L,-*] ++(2,0) node[circ,label={[shift={(-0.3,0.0)}]:{$U_c$}}]{}
;
\draw (0,8)
  to[short,-*] ++(4,0)
  to[short] ++(4,0)
;

\end{circuitikz}
\caption[ABBC Driver]{Half-Bridge $A$ switched on low, with $B,C$ switched on high creating asymmetric currents across both phases.
}
\label{fig:ABBC-A}
\end{center}
\end{figure}

For the 2-Phase circuit switched as in \cref{fig:ABBC-A} the governing equations with unknowns $i_b,i_c,U_b$ are
\begin{align}
U_b &= L_P \udt i_A + i_A (R_T + R_S + R_P) \\
U-U_b &= i_b R_T \\
U-U_b &= L_P \udt i_c + i_c (R_T + R_P) \\
i_A &= i_b + i_c
\end{align}
and rearranging 
\begin{align}
\udt i_A  &= \frac{U - i_b R_T - i_A (R_T + R_S + R_P)}{L_P} \\
\udt (i_A - i_b)  &= \frac{i_b R_T - (i_A - i_b) (R_T + R_P)}{L_P}
\end{align}
and Laplace transforming
\begin{align}
s I_A(s)  &= \frac{U - I_b(s) R_T - I_A(s) (R_T + R_S + R_P)}{L_P} \\
s \left( I_A(s) - I_b(s) \right) &= \frac{I_b(s) R_T - \left(I_A(s) - I_b(s)\right) (R_T + R_P)}{L_P}
\end{align}
and rearranging
\begin{align}
L_P s I_A(s)  &= U - I_b(s) R_T - I_A(s) (R_T + R_S + R_P) \\
L_P s \left( I_A(s) - I_b(s) \right) &= 2 I_b(s) R_T + I_b(s) R_p - I_A(s) (R_T + R_P)
\end{align}
and again
\begin{align}
R_T I_b(s) &= U - (L_P s + R_T + R_S + R_P) I_A(s)  \\
\left(L_P s + 2 R_T + R_P\right) I_b(s) &= (L_P s + R_T + R_P) I_A(s) 
\end{align}
and combining
\begin{align}
\frac{(L_P s + R_T + R_P)}{L_P s + 2 R_T + R_P} I_A(s)&= \frac{U - (L_P s + R_T + R_S + R_P) I_A(s)}{R_T}
\end{align}
and rearranging
\begin{align}
\left( \frac{(L_P s + R_T + R_P)}{L_P s + 2 R_T + R_P} + \frac{L_P s + R_T + R_S + R_P}{R_T} \right) I_A(s) &= \frac{U}{R_T}
\end{align}
and rearranging
\begin{align}
\left( R_T (L_P s + R_T + R_P) \right. \\
+ &\left (L_P s + R_T + R_S + R_P) (L_P s + 2 R_T + R_P) \right) I_A(s) \\
 = &(L_P s + 2 R_T + R_P) U
\end{align}
expanding
\begin{gather}
\begin{aligned}
\left( R_T L_P s + R_T^2 + R_P R_T \right. \\
+ & L_P^2 s^2 + R_T L_P s + R_S L_P s + R_P L_P s \\
+ & R_T L_P s + 2R_T^2 + R_P R_T \\
+ & R_S L_P s + 2 R_S R_T + R_P R_S\\
+ &\left. R_P L_P s + 2 R_P R_T + R_P^2 \right) I_A(s) \\
 = (L_P s + 2 R_T + R_P) U
\end{aligned}
\end{gather}
simplifying
\begin{gather}
\begin{aligned}
\left( L_P^2 s^2 + 2 R_S L_P s + 2 R_P L_P s + 3 R_T L_P s \right. \\
+ \left. 2 R_S R_T + R_P R_S + R_P^2 + 3 R_T^2 + 4 R_P R_T\right) I_A(s) \\
 = & (L_P s + 2 R_T + R_P) U
\end{aligned}
\end{gather}

\subsection{Resistive Static Circuit}

\begin{figure}[htbp]
\begin{center}
\begin{circuitikz} 
\draw (0,8) 
  to[R,] ++(0,-2)
  to[normal open switch,] ++(0,-1)
  to[R,] ++(0,-2)
  to[R,] ++(0,-2)
  to[normal open switch,l=$A$] ++(0,-1)
;
\draw (4,8) node[vcc]{U}
  to[R,] ++(0,-2)
  to[normal open switch,] ++(0,-1)
  to[R,] ++(0,-2)
  to[R,] ++(0,-2)
  to[normal open switch,l=$B$] ++(0,-1)
  node[rground]{}
;
\draw (8,8) 
  to[R,l=$R_T$] ++(0,-2)
  to[normal open switch,] ++(0,-1)
  to[R,l=$R_T$] ++(0,-2)
  to[R,l=$R_S$] ++(0,-2)
  to[normal open switch,l=$C$] ++(0,-1)
;
\draw (0,0)
  to[short,-*] ++(4,0)
  to[short] ++(4,0)
;
\draw (0,5)
  to[R,l=$R_P$,*-] ++(4,0)
  to[R,*-*] ++(4,0)
;
\draw (0,8)
  to[short,-*] ++(4,0)
  to[short] ++(4,0)
;

\end{circuitikz}
\caption[ABBC Driver Static]{3-Phase Driver with 2-Phase Motor static resistive circuit.}
\label{fig:ABBC-R}
\end{center}
\end{figure}

\begin{figure}[htbp]
\begin{center}
\subfloat[A switched low.]{
\begin{circuitikz} 
\draw (0,8) 
  to[R,] ++(0,-2)
  to[normal open switch,] ++(0,-1)
  to[R] ++(0,-2)
  to[R,f=$i_A$] ++(0,-2)
  to[short,l=$A$] ++(0,-1)
;
\draw (2,8) node[vcc]{U}
  to[R,f=$i_b$] ++(0,-2)
  to[short,] ++(0,-1)
  to[R,] ++(0,-2)
  to[R,] ++(0,-2)
  to[normal open switch,l=$B$] ++(0,-1)
  node[rground]{}
;
\draw (4,8) 
  to[R,l=$R_T$,f=$i_c$] ++(0,-2)
  to[short,] ++(0,-1)
  to[R,l=$R_T$,] ++(0,-2)
  to[R,l=$R_S$,] ++(0,-2)
  to[normal open switch,l=$C$] ++(0,-1)
;
\draw (0,0)
  to[short,-*] ++(2,0)
  to[short] ++(2,0)
;
\draw (0,5)
  to[R,l_=$R_P$,*-*] ++(2,0)
  to[R,-] ++(2,0) 
;
\draw (0,8)
  to[short,-*] ++(2,0)
  to[short] ++(2,0)
;

\end{circuitikz}
}%
~
\subfloat[B switched low.]{
\begin{circuitikz} 
\draw (0,8) 
  to[R,f=$i_a$] ++(0,-2)
  to[short,] ++(0,-1)
  to[R] ++(0,-2)
  to[R,] ++(0,-2)
  to[normal open switch,l=$A$] ++(0,-1)
;
\draw (2,8) node[vcc]{U}
  to[R,] ++(0,-2)
  to[normal open switch,] ++(0,-1)
  to[R,] ++(0,-2)
  to[R,f=$i_B$] ++(0,-2)
  to[short,l=$B$] ++(0,-1)
  node[rground]{}
;
\draw (4,8) 
  to[R,l=$R_T$,f=$i_c$] ++(0,-2)
  to[short,] ++(0,-1)
  to[R,l=$R_T$,] ++(0,-2)
  to[R,l=$R_S$,] ++(0,-2)
  to[normal open switch,l=$C$] ++(0,-1)
;
\draw (0,0)
  to[short,-*] ++(2,0)
  to[short] ++(2,0)
;
\draw (0,5)
  to[R,l_=$R_P$,*-*] ++(2,0)
  to[R,-] ++(2,0) 
;
\draw (0,8)
  to[short,-*] ++(2,0)
  to[short] ++(2,0)
;

\end{circuitikz}
}
\caption[ABBC-RAB]{Resistive Half-Bridge switched low on $A,B$ phases, respectively.
}
\label{fig:ABBC-RAB}
\end{center}
\end{figure}

For the 2-Phase circuit switched as in \cref{fig:ABBC-RAB} the measureable resistances are
\begin{gather}
\begin{aligned}
R_A &= R_S + R_T + R_P + \frac{R_T (R_T + R_P)}{2 R_T + R_P} \\
R_B &= R_S + R_T + \frac{R_T + R_P}{2}
\end{aligned}
\end{gather}
which allows us to solve for $R_T, R_P$ with $R_S$ being known:
\begin{gather}
\begin{aligned}
(2 R_T + R_P) (R_A - R_S - R_T - R_P) &= R_T (R_T + R_P) \\
R_P &= 2 R_B - 2 R_S - 3 R_T
\end{aligned}
\end{gather}
and combining the two equations to solve for $R_T$
\begin{gather}
\begin{aligned}
(2 R_B - 2 R_S - R_T) (R_A + R_S + 2 R_T - 2 R_B) &= R_T (2 R_B - 2 R_S - 2 R_T) \\
2 R_A R_B + 2 R_B R_S + 4 R_B R_T - 4 R_B^2 \\
 - 2 R_A R_S - 2 R_S^2 - 4 R_S R_T + 4 R_B R_S\\
 - R_A R_T - R_S R_T - 2 R_T^2 + 2R_B R_T &= 2 R_B R_T - 2 R_S R_T - 2 R_T^2 \\
2 R_A R_B - 4 R_B^2 - 2 R_A R_S - 2 R_S^2 + 6 R_B R_S &= R_A R_T + 3 R_S R_T - 4 R_B R_T\\
2 \frac{ R_A R_B - 2 R_B^2 - R_A R_S - R_S^2 + 3 R_B R_S}{R_A + 3 R_S- 4 R_B} &= R_T\\
2 \frac{ 2 R_B^2 - R_A R_B  + R_A R_S - 3 R_B R_S + R_S^2}{4 R_B - R_A - 3 R_S} &= R_T\\
\end{aligned}
\end{gather}
and for $R_P$
\begin{gather}
\begin{aligned}
2 \frac{ 2 R_B^2 - R_A R_B  + R_A R_S - 3 R_B R_S + R_S^2}{4 R_B - R_A - 3 R_S} &= \frac{R_P - 2 R_B + 2 R_S}{3} \\
\frac{ 12 R_B^2 - 6 R_A R_B  + 6 R_A R_S - 18 R_B R_S + 6 R_S^2}{4 R_B - R_A - 3 R_S} + 2 R_B - 2 R_S &= R_P \\
\frac{ 20 R_B^2 - 8 R_A R_B  + 8 R_A R_S - 32 R_B R_S + 12 R_S^2}{4 R_B - R_A - 3 R_S} &= R_P \\
4 \frac{ 5 R_B^2 - 2 R_A R_B  + 2 R_A R_S - 8 R_B R_S + 3 R_S^2}{4 R_B - R_A - 3 R_S} &= R_P
\end{aligned}
\end{gather}

\subsection{Single Current Path}

System identification  with only one active high and low switch at a time, and the third half-bridge being disabled, results in simpler equations than having two active high switches:
\begin{gather}
\begin{aligned}
R_{AB} = R_{BC} &= R_P + 2 R_T + R_S \\
R_{AC} &= 2 R_P + 2 R_T + R_S \\
\end{aligned}
\end{gather}

\subsection{2-Phase Driving}

Because the 2 phases share a common point, the maximum available voltage is limited to less than the line voltage. It is assumed that the phases are driven sinusoidally with a $\frac{\pi}{2}$ phase shift.

With a naive approach of keeping the center point at half the nominal voltage, only half the nominal voltage is available for each phase. Moving the midpoint, too, allows us to increase phase voltage to $U_P = \sqrt{2} U$, with the following waveforms:
\begin{gather}
\begin{aligned}
U_{A} &= \frac{\cos x}{\sqrt{2}} \\
U_{C} &= \frac{\sin x}{\sqrt{2}} \\
U_{B} &= \frac{\cos x + \sin x}{4} = \frac{\cos \left(x - \frac{\pi}{4}\right)}{2 \sqrt{2}}
\end{aligned}
\end{gather}
and PWM
\begin{gather}
\begin{aligned}
D_{A} &= U_{B} + U_{A} \\
D_{B} &= U_{B} \\
D_{C} &= U_{B} + U_{C}
\end{aligned}
\end{gather}

The physical limiting condition to observe is that 
\begin{gather}
\begin{aligned}
\forall \left( U_{A}+U_{B} \right) &\leq U_P
\end{aligned}
\end{gather}

\section{Motor Model}

\subsection{DC Motor State Equation}

The electrical and mechanical DC motor model with the parameters of  electrical motor constant $k_e$, rotor inertia $J$, dynamic friction $k_d$, and disturbance torque $\Gamma_d$:

\begin{gather}
\begin{aligned}
L\frac{\ud }{\ud t} \imath&= U - R \imath - k_e \omega \\
J \frac{\ud }{\ud t} \omega &= k_e \imath - k_d \omega - \Gamma_d \\
\frac{\ud}{\ud t} x &= \omega
\end{aligned}
\end{gather}

\subsection{2-Phase Stepper Motor Model}

The stepper motor model is similar to DC motor model, but takes into account the currents flowing in each phase. The number of steps per revolution is
\begin{gather}
\begin{aligned}
S &= 2 \cdot m \cdot n
\end{aligned}
\end{gather}
where $n$ is the number of pole-pairs and $m$ is the number of phases. For a typical \unit{1.8}{\degree} per step for $S=200$ and $m=2$, it follows that there are $n=50$ pole-pairs.

Assuming a sinusoidal magnetic characteristic the torque contribution from each phase is
\begin{gather}
\begin{aligned}
\tau_j &= k_m \sin \left( n \theta_m + \phi_{0j}\right) \cdot \imath_j
\end{aligned}
\end{gather}
where $\theta_m$ is the mechanical angle of the rotor and $\phi_{0j}$ is the phase offset. The model is very similar to the DC motor\footnote{we use a 2-phase PM motor model} except that the torque is the sum of the phase torques
\begin{gather}
\begin{aligned}
J \frac{\partial }{\partial t} \omega &= \sum_j\tau_j - k_d \omega_m - \Gamma_d \\
\sum_j \tau_j &= k_m I \sin \phi_m
\end{aligned}
\end{gather}
The current is a function of the applied voltage and motor back-EMF\footnote{The electrical equations are valid for any number of phases}
\begin{gather}
\begin{aligned}
\label{eq:motphase} U_j &= E_j + R \imath_j + L \frac{\partial \imath_j}{\partial t} \\
E_j &= k_e \omega_m \cos \left( n \theta_m + \phi_{0j} \right) = k_e \omega_m \cos \left( \theta_{ej} + \phi_m \right)
\end{aligned}
\end{gather}
Further ignoring the winding offsets, all phases behave the same. The only unknowns in \cref{eq:motphase} after electrical parameter identification of $R,L$ are $k_e$, and $\phi_m$, as $U$, $\imath$, and $\omega_m$ are directly observed.

It is noteworthy that $E$ is phase-shifted by $\phi_m$, but it's magnitude is independent of it, thus the RMS value $E_{\mathrm{RMS}}$ of $E$ is independent of $\phi_m$ being
\begin{gather}
\begin{aligned}
E_{\mathrm{RMS}} &= \frac{1}{\sqrt{2}} k_e \omega_m
\end{aligned}
\end{gather}

For a constant $\omega$, we can look at the phase relationships
\begin{gather}
\begin{aligned}
\mathbf{E} &= \mathbf{U} - \mathbf{Z} \mathbf{\imath} \\
k_e \omega_m \cos \left( \theta_{e} + \phi_m \right) &= U \cos(\theta_{e} + \phi_e) - R I \cos(\theta_e) - LI \sin(\theta_e) \\
k_e \omega_m e^{j \phi_m}  &= U e^{j \phi_e} - R I - LI e^{j \pi/2}
\end{aligned}
\end{gather}

%Thus
%\begin{gather}
%\begin{aligned}
%U_j &= k_m \cos \left( n \theta_m + \phi_{0j} \right) \omega_m + R I \cos \left( \theta_e + \phi_{0j} \right) - L I \sin \left( \theta_e + \phi_{0j} \right) \\
%\phi_Z &= \arctan\left(\frac{L}{R}\right) \\
%\phi_m &= n\theta_m - \theta_e \\
%U_j &= k_m \omega_m\cos \left( n \theta_m + \phi_{0j} \right) + Z I \cos \left( n\theta_m + \phi_{0j} + \phi_Z - \phi_m \right) \\
%\tan \varphi &= \frac{ZI\sin(\phi_Z-\phi_m)}{k_m \omega_m + ZI\cos(\phi_Z-\phi_m)} \\
%U_j &= \sqrt{ k_m^2\omega_m^2 + Z^2I^2  + 2 k_m \omega_m Z I \cos \left(\phi_m - \phi_Z \right)} \cos \left( n \theta_m + \phi_{0j} + \varphi \right)
%\end{aligned}
%\end{gather}

\subsubsection{Parameter Estimation}

\begin{table}[htbp]
\caption{Motor parameter estimation steps.}
\begin{center}
\begin{tabular}{llp{0.5\textwidth}} \toprule
 \multicolumn{2}{l}{Parameter} & Estimation Condition \\
\midrule
$R$ & winding resistance & static current\\
$L$ & winding inductance & dynamic current\\
$k_e$ & el.\ motor constant & constant speed\\
$k_d$ & dynamic friction & variable speed\\
$k_s$ & static friction & ???\\
? & encoder offset & variable position\\
$t_?$ & encoder delay & ???\\
$\phi_m$ & load angle & constant speed \\
\bottomrule
\end{tabular}
\end{center}
\label{tab:paramest}
\end{table}%

$R,L$ can be determined by mechanically static (no significant rotation) tests, as they are purely a function of the electrical circuit. 

The back-EMF can be determined through change of $i_{\textrm{RMS}}$ when applying a constant-voltage with different speeds. Though $U, \imath, E$ are all synchronous, they will not be in the same phase.
\begin{gather}
\begin{aligned}
U_j &= \sqrt{ k_m^2\omega_m^2 + Z^2I^2  + 2 k_m \omega_m Z I \cos \left(\phi_m - \phi_Z \right)} \cos \left( n \theta_m + \phi_{0j} + \varphi \right) \\
U_{\textrm{RMS}} &= \frac{1}{\sqrt{2}} \sqrt{ k_m^2\omega_m^2 + Z^2I^2  + 2 k_m \omega_m Z I \cos \left( \phi_m - \phi_Z \right)}
\end{aligned}
\end{gather}
$k_m$ and $\phi_m$ are unknowns. $\phi_m$ depends on the motor's load condition, but can be eliminated in approximations. For $\omega = 0$, this is just the familiar
\begin{gather}
\begin{aligned}
U_{\textrm{RMS}} &= \frac{1}{\sqrt{2}} ZI
\end{aligned}
\end{gather}
and for $\omega \gg 0$, as $\phi_m$ approaches \unit{90}{\degree}
\begin{gather}
\begin{aligned}
U_{\textrm{RMS}} &\approx \frac{1}{\sqrt{2}} k_m \omega_m
\end{aligned}
\end{gather}

Assuming viscous friction only, is there a speed with a minimum current for constant voltage pwm before stall due to the interaction of EMF and phase lag?
\begin{gather}
\begin{aligned}
k_m I \sin \phi_m &= k_d \omega_m \\
\sin \phi_m &= \frac{k_d \omega_m}{k_m I} \\
2 U^2_{\textrm{RMS}} &= k_m^2\omega_m^2 + Z^2I^2  + 2 k_m \omega_m Z I \cos \left( \phi_m - \phi_Z \right)\\
0 & = Z^2I^2  + 2 k_m \omega_m Z I \cos \left( \phi_m - \phi_Z \right) + k_m^2\omega_m^2 - 2 U^2_{\textrm{RMS}} \\
I &= \frac{-2 k_m \omega_m Z \cos \left( \phi_m - \phi_Z \right) \pm \sqrt{4 k^2_m \omega^2_m Z^2 \cos^2 \left( \phi_m - \phi_Z \right) - 4 Z^2 \left( k_m^2\omega_m^2 - 2 U^2_{\textrm{RMS}} \right)}}{2 Z^2} \\
I &= \frac{-k_m \omega_m \cos \left( \phi_m - \phi_Z \right) \pm \sqrt{k^2_m \omega^2_m \left(\cos^2 \left( \phi_m - \phi_Z \right) - 1\right) + 2 U^2_{\textrm{RMS}} }}{Z} \\
I &= \frac{-k_m \omega_m \cos \left( \phi_m - \phi_Z \right) \pm \sqrt{k^2_m \omega^2_m \sin^2 \left( \phi_m - \phi_Z \right) + 2 U^2_{\textrm{RMS}} }}{Z}
\end{aligned}
\end{gather}
splitting $\cos \left( \phi_m - \phi_Z \right)$ via harmonic addition
\begin{gather}
\begin{aligned}
\cos \left( \phi_m - \phi_Z \right)&= \frac{1}{Z} \left( R\cos \phi_m + L \sin \phi_m \right) \\
%- \phi_Z &= \arctan \left( - \frac{L}{R} \right) \\
\rho &= \frac{k_d \omega_m}{k_m I} \\
\cos \left( \phi_m - \phi_Z \right)&= \frac{1}{Z} \left( R \sqrt{1-\rho^2} + L \rho \right) \\
2 k_m \omega_m I \left( R \sqrt{1-\rho^2} + L \rho \right) &= 2 k_d \omega_m^2 L + 2 k_m \omega_m I R \sqrt{1-\rho^2}\\
&= 2 k_d \omega_m^2 L + 2 k_m \omega_m R \sqrt{I^2-I\frac{k_d^2 \omega_m^2}{k_m^2}} \\
2 k_m \omega_m R \sqrt{I^2-I\frac{k_d^2 \omega_m^2}{k_m^2}}& = 2 U^2_{\textrm{RMS}} -k_m^2\omega_m^2 - Z^2I^2  - 2 k_d \omega_m^2 L \\
\end{aligned}
\end{gather}
differentiating wrt $\omega$ to find minima/maxima
\begin{gather}
\begin{aligned}
\frac{\partial}{\partial \omega_m} 2 k_m \omega_m R \sqrt{I^2-I\frac{k_d^2 \omega_m^2}{k_m^2}}& = \frac{\partial}{\partial \omega_m} \left( -k_m^2\omega_m^2 - 2 k_d \omega_m^2 L \right)\\
2 k_m R \sqrt{I^2-I\frac{k_d^2 \omega_m^2}{k_m^2}} +  2 R  \left(I^2-I\frac{k_d^2 \omega_m^2}{k_m^2}\right)^{-\frac{1}{2}} I\frac{k_d^2 \omega_m^2}{k_m} & =   - 2k_m^2\omega_m - 4 k_d \omega_m L \\
R \sqrt{k_m^2 I^2-I k_d^2 \omega_m^2} +  R  \left(k_m^2 I^2 - I k_d^2 \omega_m^2\right)^{-\frac{1}{2}} I k_d^2 \omega_m^2  & = - k_m^2\omega_m - 2 k_d \omega_m L \\
\end{aligned}
\end{gather}
\begin{gather}
\begin{aligned}
R \left(k_m^2 I^2 - I k_d^2 \omega_m^2 \right) +  R I k_d^2 \omega_m^2  & = - R \sqrt{k_m^2 I^2-I k_d^2 \omega_m^2} \left(k_m^2\omega_m - 2 k_d \omega_m L \right) \\
R k_m^2 I^2  & = - R \sqrt{k_m^2 I^2-I k_d^2 \omega_m^2} \left(k_m^2\omega_m - 2 k_d \omega_m L \right) \\
R^2 k_m^4 I^4  & = R^2 \left( k_m^2 I^2-I k_d^2 \omega_m^2 \right) \left(k_m^2\omega_m - 2 k_d \omega_m L \right)^2 \\
k_m^4 I^3  & = \omega_m^2 \left( k_m^2 I - k_d^2 \omega_m^2 \right) \left(k_m^2 - 2 k_d \right)^2 \\
k_m^4 I^3   - \omega_m^2 k_m^2 \left(k_m^2 - 2 k_d \right)^2 I & = - k_d^2 \omega_m^4  \left(k_m^2 - 2 k_d \right)^2 \\
\end{aligned}
\end{gather}
is a depressed cubic that can be solved with Cardano's formula
\begin{gather}
\begin{aligned}
k_m^4 I^3 - \omega_m^2 k_m^2 \left(k_m^2 - 2 k_d \right)^2 I & = - k_d^2 \omega_m^4  \left(k_m^2 - 2 k_d \right)^2 \\
p &= - \omega_m^2 k_m^2 \left(k_m^2 - 2 k_d \right)^2 \\
q &= \omega_m^4  \left(k_m^2 - 2 k_d \right)^2 \\
q^2/4 + p^3/27 &= \frac{1}{4} k_d^4 \omega_m^8  \left(k_m^2 - 2 k_d \right)^4 - \frac{1}{3^3} \omega_m^6 k_m^6 \left(k_m^2 - 2 k_d \right)^6 \\
q^2/4 + p^3/27 &= \omega_m^6 \left(k_m^2 - 2 k_d \right)^4 \left(\frac{1}{4}k_d^4 \omega_m^2   - \frac{1}{3^3} k_m^6 \left(k_m^2 - 2 k_d \right)^2 \right) \\
\sqrt{q^2/4 + p^3/27} &= \omega_m^3 \left(k_m^2 - 2 k_d \right)^2 \sqrt{\frac{1}{4}k_d^4 \omega_m^2- \frac{1}{3^3} k_m^6 \left(k_m^2 - 2 k_d \right)^2 } \\
\end{aligned}
\end{gather}

solving for $\omega$
\begin{gather}
\begin{aligned}
0 &= k_d^2 \omega_m^4  \left(k_m^2 - 2 k_d \right)^2   - \omega_m^2 k_m^2 \left(k_m^2 - 2 k_d \right)^2 I + k_m^4 I^3 \\
\end{aligned}
\end{gather}

\begin{gather}
\begin{aligned}
\sin \left( \phi_m - \phi_Z \right)&= \sin \phi_m \cos \phi_Z - \cos \phi_m \sin \phi_Z \\
\sin^2 \left( \phi_m - \phi_Z \right)&= \sin^2 \phi_m \cos^2 \phi_Z + \cos^2 \phi_m \sin^2 \phi_Z - 2 \sin \phi_m \cos \phi_Z \cos \phi_m \sin \phi_Z\\
\rho &= \frac{k_d \omega_m}{k_m I} \\
\sin^2 \left( \phi_m - \phi_Z \right)&= \rho^2 \cos^2 \phi_Z + \left( 1-\rho^2 \right) \sin^2 \phi_Z - 2 \rho \cos \phi_Z \sqrt{1-\rho^2} \sin \phi_Z
\end{aligned}
\end{gather}
aproximating $\phi_Z \approx 0$
\begin{gather}
\begin{aligned}
\sin^2 \left( \phi_m - \phi_Z \right)&= \rho^2 \\
%\sin^2 \left( \phi_m - \phi_Z \right)&= \sin^2 \phi_m \cos^2 \phi_Z + \left(1 - \sin^2 \phi_m \right) \sin^2 \phi_Z - 2 \sin \phi_m \cos \phi_Z \cos \phi_m \sin \phi_Z\\
 I &= \frac{\mp k_m \omega_m \left(1 - \sin^2 \left( \phi_m - \phi_Z \right) \right) \pm \sqrt{k^2_m \omega^2_m \sin^2 \left( \phi_m - \phi_Z \right) + 2 U^2_{\textrm{RMS}} }}{Z} \\
 I &= \frac{\mp k_m \omega_m \left(1 - \rho^2 \right) \pm \sqrt{k^2_m \omega^2_m \rho^2 + 2 U^2_{\textrm{RMS}} }}{Z}
\end{aligned}
\end{gather}

\subsection{Observability}

Ideally, our motor model perfectly captures all relevant properties needed to control torque, velocity, and positioning. However, that will never truly be the case, so we rely on estimating parameters for known relationships, and accounting for unknowns with black-box parameters.

We typically treat a motor model as static, and do not change the "fixed" parameters while we're controlling the motor, and only try to account for some variables like a varying or unknown load.

Apart from the electrical motor itself, a given machine might allow further modeling to increase the model's fidelity, and thus control accuracy and precision. For example, a robot arm's mass, inertia, and the influence of gravity can be modeled in the controller instead of assuming a black-box load.

As we increase the number of parameters, it might not be possible to estimate parameters, even for known configurations, if we don't have the required sensors.

\subsection{Parameter Estimation through a Kalman Filter}

If we model the motor parameters as state variables of a Kalman Filter, the filter's process and measurement covariance matrices $\mQ, \mR$ should include all the information necessary to improve parameter estimates at runtime, as long as we can approximate them well enough.

\section{Motor Discovery Implementation}

The implementation / parameter estimation is implemented as:
\begin{enumerate}
\item For each bridge, do a static test
    \begin{enumerate}
    \item apply large single-phase current to align rotor, wait to settle down mechanically, then zero current
    \item apply full voltage and measure current and measure current ramp to threshold current
    \item apply steady-state low duty cycle PWM and measure current for resistance estimate
    \end{enumerate}
\end{enumerate}

\section{Position Estimation}

\subsection{Discrete Kalman Filter}

\subsubsection{Difference Equation}

Variable names after \cite{kalman-tut} with slight adjustments. The discrete stochastic time-variant system is described by
\begin{gather}
\begin{aligned}
\vx_k &= \mA_{k} \vx_{k-1} +  \mB_{k} \vu_{k-1} + \vw_{k-1} \\
\vz_k &= \mH_k \vx_k + \vv_k
\end{aligned}
\end{gather}
where \vx\ is the state vector, \vu\ is the input vector, \vz\ is the observation vector, and \vw\ and \vv\ are the process and measurement noise vector vectors, respectively, for a given time step $k$.

$\mH$ maps the state to the observable variables, and features prominently in the Kalman Filter equations.

The noise vectors are defined by the corresponding covariance matrices $\mQ_k$ and $\mR_k$. The state covariance matrix is $\mP_k$.

\subsubsection{Canonical Kalman Filter Update}

The first part of the update is prediction
\begin{gather}
\begin{aligned}
\vx^-_k &= \mA \vx^+_{k-1} +  \mB \vu_{k-1} \\
\mP^-_k &= \mA\mP^+_{k-1}\mA^T + \mQ
\end{aligned}
\end{gather}
which results in the \em a-priori \em (as in before measurement) estimates of $\vx^-, \mP^-$. The second part is the correction through measurement
\begin{gather}
\begin{aligned}
\mK &= \mP^-_k\mH^T\left( \mH \mP^-_k \mH^T + \mR \right)^{-1}\\
\vx^+_k &= \vx^-_k + \mK \left(\vz_k - \mH\vx^-_k \right)\\
\end{aligned}
\end{gather}
resulting in the \em Kalman Gain \em $\mK$, and \em a-posteriori \em (post measurement) estimates of the state vector $\vx^+$. In this form, the computation of $\mK$ requires a matrix inversion. If the process and measurement noise covariance matrices are constant, the inversion can be avoided by pre-computing the state covariance matrix $\mP$ with the Ricatti Equation. In our case, however, both $\mQ$ and $\mR$ are time-dependent.

The final step is updating the state covariance $\mP$, which for the optimal Kalman gain is simplified
\begin{gather}
\begin{aligned}
\mP^+_k &= \left( \mI - \mK \mH \right) \mP^-_k
\end{aligned}
\end{gather}
or the more numerically robust \em Joseph form,\em which preserves symmetry even in case of numerical rounding errors:
\begin{gather}
\begin{aligned}
\mP^+_k &= \left( \mI - \mK \mH \right) \mP^-_k \left( \mI - \mK \mH \right)^T + \mK \mR \mK^T
\end{aligned}
\end{gather}

\subsubsection{Sequential Kalman Filter}

The sequential Kalman filter applies measurements one at a time, instead of all at once, resulting in some numerical simplification.

Reformulating the correction step in terms of the measurement prediction covariance $\mS$:
\begin{gather}
\begin{aligned}
\mS &= \mH \mP^-_k \mH^T + \mR \\
\mK &= \mP^-_k\mH^T \mS^{-1}
\end{aligned}
\end{gather}
allows us to see that for each scalar measurement $z_i$, with scalar covariance $r_i$ the measurement prediction covariance also becomes scalar, and thus
\begin{gather}
\begin{aligned}
s_i &= \mH \mP^-_k \mH^T + r_i \\
\mK_i &= \frac{\mP^-_k\mH^T}{s_i}
\end{aligned}
\end{gather}
for each measurement.

With a single measurement, we only need a subset of $\mH$, as our input vector $\vz$ is reduced to a single scalar, and thus we only need the part of $\mH$ mapping $z_i$ to $\vx$. This also reduces the dimension of $\mK$ accordingly.
\begin{gather}
\begin{aligned}
\mH &= \left\{ \begin{array}{c} \vh_0 \\
\vh_i \\
\cdots \\
\end{array} \right\} \\
s_i &= \vh_i \mP^-_k \vh_i^T + r_i \\
\vk_i &= \frac{\mP^-_k \vh_i^T}{s_i} \\
\vx^+ &= \vx^- + \vk_i \left(z_{i} - \vh_i \vx^- \right) \\
\mP^+ &= \left( \mI - \vk_i \vh_i \right) \mP^- \left( \mI - \vk_i \vh_i \right)^T + \vk_i \vk_i^T r_i
\end{aligned}
\end{gather}

\subsubsection{Simplest Approximation Difference Equations}

In the simplest possible form, the motor can be treated as an inertial mass without outside forces, eg.{} it having constant speed.

\begin{gather}
\begin{aligned}
\omega &= \frac{\ud}{\ud t} x
\end{aligned}
\end{gather}

This is a useful approximation if further motor parameters that link the electrical and mechanical models are unknown, but has the big drawback that changes in speed cannot be modeled well. Therefore, this model is only useful to determine motor position and speed from the position encoder during system identification, but not during regular operation.

The mechanical position $x$ of the motor and its speed $\omega$ compromise the state vector. There are no inputs, and the only available measurement is the measured position $x'$:
\begin{gather}
\begin{aligned}
\vx &= \left(
\begin{array}{c}
      x  \\
 \omega \\
%\ddot{x}   
\end{array}
\right) \\
%\vu &= \left(
%\begin{array}{c}
%      \imath
%\end{array}
%\right) \\
\vz &= \left(
\begin{array}{c}
      x'
\end{array}
\right)
\end{aligned}
\end{gather}
The update/correction matrices depend only on the time step size $h$:
\begin{gather}
\begin{aligned}
\mA &= \left(
\begin{array}{cc}
 1 & h \\
 0 & 1 \\
\end{array}
\right) \\
%\mB &= \left(
%\begin{array}{c}
% k_T \frac{h^2}{2} \\
% k_T h   
%\end{array}
%\right) \\
\mH &= \left(
\begin{array}{c c}
 1 & 0
\end{array}
\right).
\end{aligned}
\end{gather}
Without inputs, $\mB\vu = 0$ and can be ignored.

The covariance matrices are the most difficult to determine. We need to take into account the effects of the applied voltage $U$ and/or current $\imath$, and balance the model and measurement covariances to get a stable prediction, but also a fast enough reaction, though such a filter will invariable react more slowly to changes than a more complete model. In addition to $h$, we might also consider the change in input voltage $\frac{\ud}{\ud t} U$ and time since the last observation $\lambda$
\begin{gather}
\begin{aligned}
%\mP &= \left(
%\begin{array}{cc}
% ? & 0 \\
% 0 & ? \\
%\end{array}
%\right) \\
\mQ &= \left(
\begin{array}{cc}
 \left( k_{Q1} h \right)^2 & 0 \\
 0 & \left( k_{Q2} h \right)^2
\end{array}
\right) \\
\mR &= \left(
\begin{array}{c}
 \left( k_{R1} + k_{R2} \lambda + k_{R3} \omega \lambda \right)^2\\
\end{array}
\right)
\end{aligned}
\end{gather}
For $\mR$, we will have a noise figure from the sensor to determine $k_{R1}$. $k_{R2}$ expresses how much we trust the measurement as time goes on without further information, and $k_{R2}$ expresses uncertainty it terms of rotational speed.

If the motor that isn't being driven, what is the expected amount we expect it to move? For a stepper motor, we expect it might clog to the next full step. If it is moving, and we expect it to continue so without further input, it will have moved $\omega \lambda$ plus some unmodeled effect from potential friction. 

The uncertainty in the process might quantified by taking into account potential forces that are not accounted for in the model. Neglecting external forces, we have control over our target speed $\omega$ and the acceleration $\alpha_{\textrm{max}}$.

For a scalar $R$, due to only having a single observed variable, $\mK$ can be calculated straight-forwardly without a matrix inversion.

\begin{table}[htbp]
\caption{Covariance parameters for constant speed motor model.}
\begin{center}
\begin{tabular}{llp{0.5\textwidth}} \toprule
 Parameter & Value & Comment \\
\midrule
$k_{Q1}$ & $0.2\pi$ & \unit{10}{\%} of $\alpha_{\textrm{max}}$ as unmodeled disturbance\\
$k_{Q2}$ & $2\pi$ & larger uncertainty in speed, due it being derived from position\\
$k_{R1}$ & $0.0222$  & ONL $\sigma = \unit{0.068}{\degree}$ + INL $ = \unit{1.2}{\degree}$\\
$k_{R2}$ & $2\pi$ & $\alpha_{\textrm{max}} = \unit{2\pi}{\radian\per\second\squared}$ acc limit \\
$k_{R3}$ & $0$ & assuming measurement is compensated by speed est. \\
\bottomrule
\end{tabular}
\end{center}
\label{tab:cov-params-const-speed}
\end{table}%

\section{Cogging}

PMSM type motors, including BLDCs, exhibit a phenomenon known as cogging: because of the permanent magnets, even when unenergized, the rotor experience a non-constant torque as it rotates, pulling it towards certain positions that maximize magnetic flux between the rotor and the stator.

\subsection{Cogging Model}

\begin{figure}[htbp]
\begin{center}
\begin{tikzpicture}[>=latex]
	\tikzstyle{spring}=[thick,decorate,decoration={zigzag,pre length=4,post length=4,segment length=6}]
	\tikzstyle{ground}=[fill,pattern=vertical lines,draw=none,minimum width=0.75cm,minimum height=0.3cm,inner sep=0pt,outer sep=0pt]

	% axis
	\draw[thick,->] (-1,3) node[anchor=east]{$\theta_e$} -- ++( 2.2, 0);
	\draw[thick,->] (-1,2.5) node[anchor=east]{$n\theta_m$} -- ++( 1.2, 0);

	% connecting node
	\node[shape=rectangle,draw,minimum size=0.05cm] (A) at (0.2,2) {};
	\node[shape=rectangle,draw] (B) at (1.2,2) {};
	\draw[dashed] (B.north) -- ( 1.2, 3.2);
	\draw[dashed] (A.north) -- ( 0.2, 2.7);
	\draw (A.west) node[anchor=east] {M};
	\draw (B.east) node[anchor=west] {E};
    % pin
	\draw (-1,1) -- ++( 1, -1) -- ++( 1, 1) -- ++( 1, -1);
    \draw[spring,>=open triangle 90,->,thick,decoration={zigzag,segment length=5}] (A.south) -- (0.2,0.2) node[pos=0.3,right] {$k_{\mathrm{cog}}$};
    % torque
    \draw[spring,-,thick,decoration={zigzag,segment length=3}] (A.east) -- (B.west) node[pos=0.5,above] {$k_{\tau}$};
%   	\draw[->] (-3,0) -- (3,0); % node[anchor=south west] {$\mathbf{\mu}$};
	% notches
	\fill[ground] (-1,1) -- ++( 1, -1) -- ++( 1, 1) -- ++( 1, -1) -- ++( 0.0, -0.333) -- ++( -1, 1) -- ++( -1, -1)  -- ++( -1, 1) -- cycle;
	\draw (-1,1) -- ++( 1, -1) -- ++( 1, 1) -- ++( 1, -1);

\end{tikzpicture}
\caption[Linear Cogging Model]{Linear cogging model similar to a pin-tumbler lock. The pin is connected to (M) with a compression spring, while (M) is connected to (E) with a tension spring. (M) represents the mechanical movement, while (E) represents the magnetic field rotation. $\theta_e - n\theta_m$ is the torque angle, and the higher it is, the more force is applied towards compressing the pin spring, and thus to move (M) towards (E).}
\label{fig:cogmod}
\end{center}
\end{figure}

A linear cogging model as shown in \cref{fig:cogmod} can work as first approximation, and highlights the main problem with cogging compensation: for a rotor position $\theta_m$ close the inflection point between one cog and the next, hysteresis is introduced in the electrical angle $\theta_e$ for the same mechanical position, depending on which direction the transition is approached from.

The good news is that under load, the instability around the inflection is reduced in effect.

The cogging torque must be compensated by either modulating the motor current amplitude and phase. Based on the single phase winding model \cref{eq:singlephase}, the speed of current change
\begin{gather}
\begin{aligned}
\label{eq:didt-winding} 
\frac{\partial \imath}{\partial t} = \frac{U - E - R \imath}{L}
\end{aligned}
\end{gather}
can tell us how fast the system can react for a given operating point. The equation shows that the available voltage $U_d = U - E - R i$ is the only variable parameter that determines ${\partial \imath} / {\partial t}$.

Both phase and amplitude modulation are limited by ${\partial \imath} / {\partial t}$, and in practice it seems like it should make sense to keep the torque angle at a maximum for most effective torque modulation, but cogging introduces non-linear effects. 

\subsubsection{Characterizing Cogging}

Cogging typically pulls a hybrid or permanent magnet motor into the next step position, which would be the same as fully energizing the corresponding motor phase. For a 3-phase configuration from \cref{fig:star}, as shown in the phase diagram \cref{fig:waveform3}, these rest points correspond to $\lambda_k = \frac{1}{3}\pi k$. Moving the current phase away from the rest point by $\Delta \theta_e$, the mechanical phase $\Delta n\theta_m$ will move a reduced amount, due to the cogging torque holding the rotor in place.

\begin{figure}[htbp]
\begin{center}
\begin{tikzpicture}[>=latex]
	\begin{axis}[
	width=0.667\textwidth,
	height=0.333\textwidth,
	title=3-Phase Cogging Torque, xlabel={$n\theta_m$}, ylabel={$\tau$}, xmin=0, xmax=2*pi, clip=false,
	axis equal=true,
	enlarge x limits=false,
	xmajorgrids,
	ymajorgrids,
	yminorgrids,
	xtick={0,pi/3, 2*pi/3, pi, 4/3*pi, 5/3*pi, 2*pi},
	xticklabels={{$\frac{0}{3}\pi$}, {$\frac{1}{3}\pi$}, {$\frac{2}{3}\pi$}, {$\frac{3}{3}\pi$}, {$\frac{4}{3}\pi$}, {$\frac{5}{3}\pi$}, {$\frac{6}{3}\pi$}},
	ytick={-3, -sqrt(3), -1, 0, 1, sqrt(3), 3},
	yticklabels={{$-3$}, {$-\sqrt{3}$}, {$$}, {$0$}, {$$}, {$\sqrt{3}$}, {$3$}},
	minor ytick={-3,-2,-1,0,1,2,3},
	major y grid style={dashed,very thin},
	major x grid style={very thin},
	minor y grid style={very thin},
	]
	% phase currents
%	\addplot[domain=0:2*pi,samples=361,red!40!black] {cos(deg(x))} node [pos=1,pin=3:{$A$}] {};
%	\addplot[domain=0:2*pi,samples=361,green!40!black] {cos(deg(x)+120)} node [pos=1,pin=-30:{$B$}] {};
%	\addplot[domain=0:2*pi,samples=361,blue!40!black] {cos(deg(x)+240)} node [pos=1,pin=30:{$C$}] {};

	% cogging torque
	\addplot[domain=0:2*pi,samples=361,black,thick] {-sin(deg(6*x))/6} node [pos=1,pin=-45:{$\tau_{\textrm{cog}}$}] {};
\end{axis}
\end{tikzpicture}

\caption[3-Phase Cogging]{3-phase cogging torque $\tau_{\textrm{cog}}$ in relation to mechanical angle $n\theta_m$.}
\label{fig:cog3}
\end{center}
\end{figure}

A decent first-order approximation of the cogging torque is $\tau_{\textrm{cog}} = - k_{\textrm{cog}} \sin \left( 6 \theta_e \right)$, as shown in \cref{fig:cog3}. The torque $\tau_e$ for a given electrical position $\theta_e$, measured mechanical position $n\theta_m$, electrical current $i$, and motor constant $k$ can be computed as 
\begin{gather}
\begin{aligned}
\tau = i k \left( \theta_e - n \theta_m \right).
\end{aligned}
\end{gather}

\begin{figure}[htbp]
\begin{center}
\begin{tikzpicture}[>=latex]
	\begin{axis}[
	width=0.667\textwidth,
	height=0.7\textwidth,
	title=3-Phase Cogging, xlabel={$\theta_e$}, ylabel={$n\theta_m$}, xmin=0, xmax=2*pi, clip=false,
	axis equal=true,
	enlarge x limits=false,
	enlarge y limits=false,
	xmajorgrids,
	ymajorgrids,
	xtick={0,pi/3, 2*pi/3, pi, 4/3*pi, 5/3*pi, 2*pi},
	xticklabels={{$\frac{0}{3}\pi$}, {$\frac{1}{3}\pi$}, {$\frac{2}{3}\pi$}, {$\frac{3}{3}\pi$}, {$\frac{4}{3}\pi$}, {$\frac{5}{3}\pi$}, {$\frac{6}{3}\pi$}},
	ytick={0,pi/3, 2*pi/3, pi, 4/3*pi, 5/3*pi, 2*pi},
	yticklabels={{$\frac{0}{3}\pi$}, {$\frac{1}{3}\pi$}, {$\frac{2}{3}\pi$}, {$\frac{3}{3}\pi$}, {$\frac{4}{3}\pi$}, {$\frac{5}{3}\pi$}, {$\frac{6}{3}\pi$}},
	major y grid style={very thin},
	major x grid style={very thin},
	]
	% phase currents
%	\addplot[domain=0:2*pi,samples=361,red!40!black] {cos(deg(x))} node [pos=1,pin=3:{$A$}] {};
%	\addplot[domain=0:2*pi,samples=361,green!40!black] {cos(deg(x)+120)} node [pos=1,pin=-30:{$B$}] {};
%	\addplot[domain=0:2*pi,samples=361,blue!40!black] {cos(deg(x)+240)} node [pos=1,pin=30:{$C$}] {};

	\addplot[domain=0:0.75*pi/6,samples=361,red!40!black,thick] {0.5/0.75*x};
	\addplot[domain=0.75*pi/6:2.75*pi/6,samples=361,red!40!black,thick] {0.5/0.75*x+0.5/0.75*pi/6};
	\addplot[domain=2.75*pi/6:4.75*pi/6,samples=361,red!40!black,thick] {0.5/0.75*x+1.0/0.75*pi/6};
	\addplot[domain=4.75*pi/6:6.75*pi/6,samples=361,red!40!black,thick] {0.5/0.75*x+1.5/0.75*pi/6};
	\addplot[domain=6.75*pi/6:8.75*pi/6,samples=361,red!40!black,thick] {0.5/0.75*x+2.0/0.75*pi/6};
	\addplot[domain=8.75*pi/6:10.75*pi/6,samples=361,red!40!black,thick] {0.5/0.75*x+2.5/0.75*pi/6};
	\addplot[domain=10.75*pi/6:12.0*pi/6,samples=361,red!40!black,thick] {0.5/0.75*x+3.0/0.75*pi/6};

	% cogging torque
	\addplot[domain=0:2*pi,samples=361,black] {-sin(deg(6*x))/6} node [pos=1,pin=-45:{$\tau_{\textrm{cog}}$}] {};
\end{axis}
\end{tikzpicture}
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

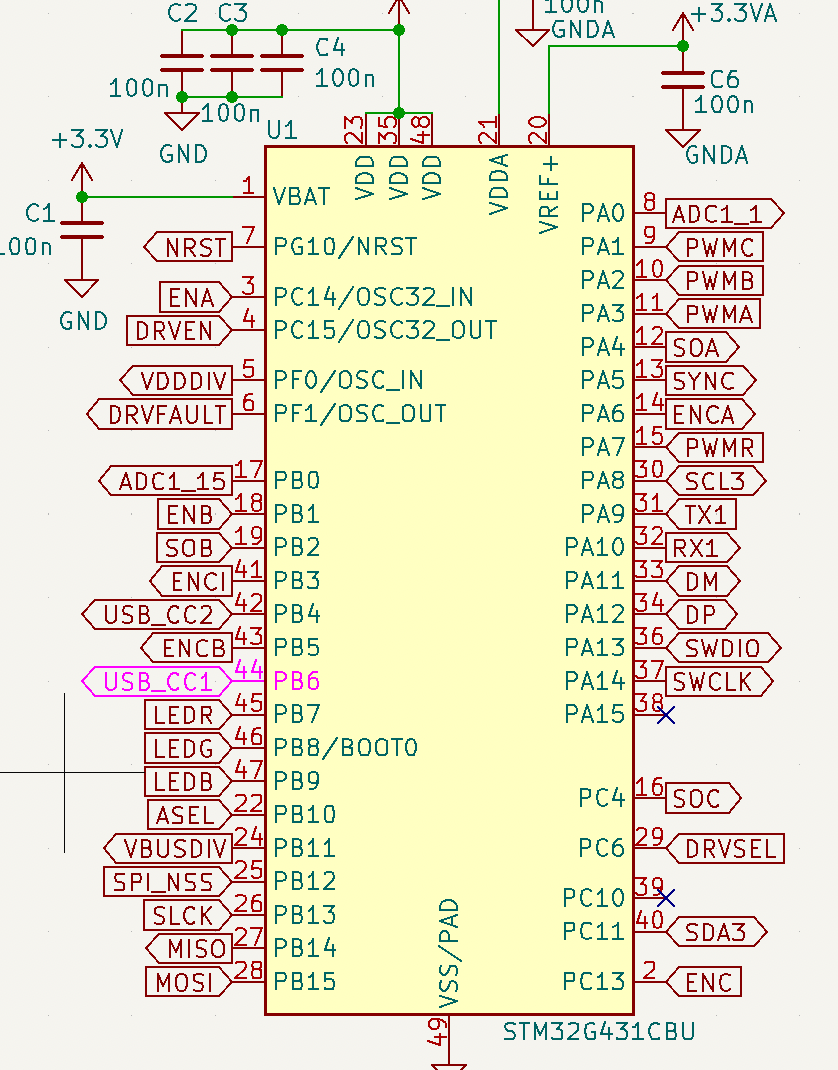
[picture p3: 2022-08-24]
hardware/smol-servo-tmc6200/v0.7.0 planned pinout schem.png

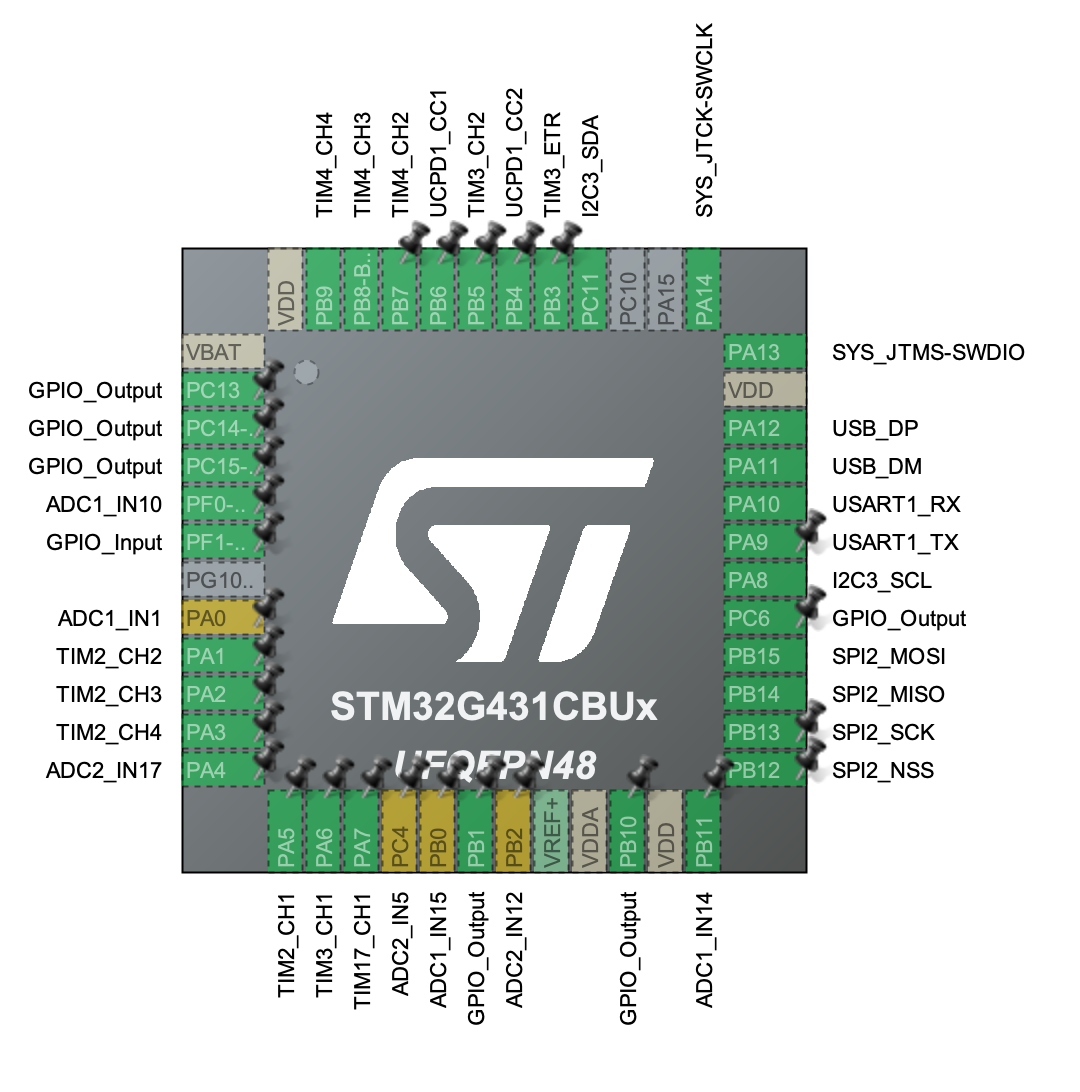
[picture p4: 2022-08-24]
hardware/smol-servo-tmc6200/v0.7.0 planned pinout.png

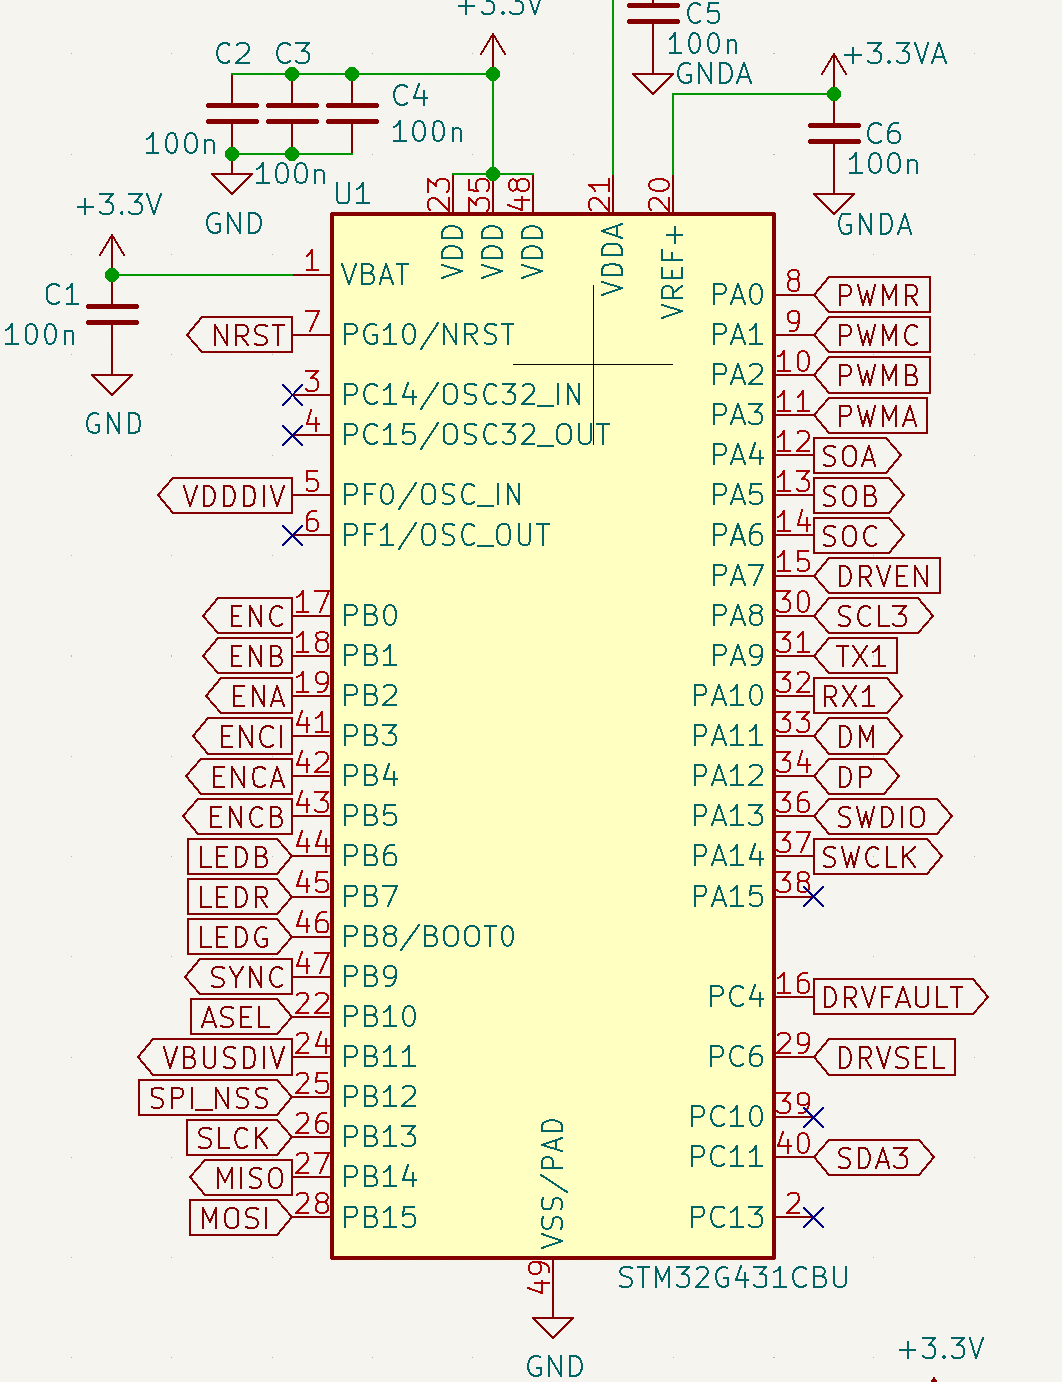
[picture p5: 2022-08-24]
hardware/smol-servo-tmc6200/v0.6.1 pinout schematic.png

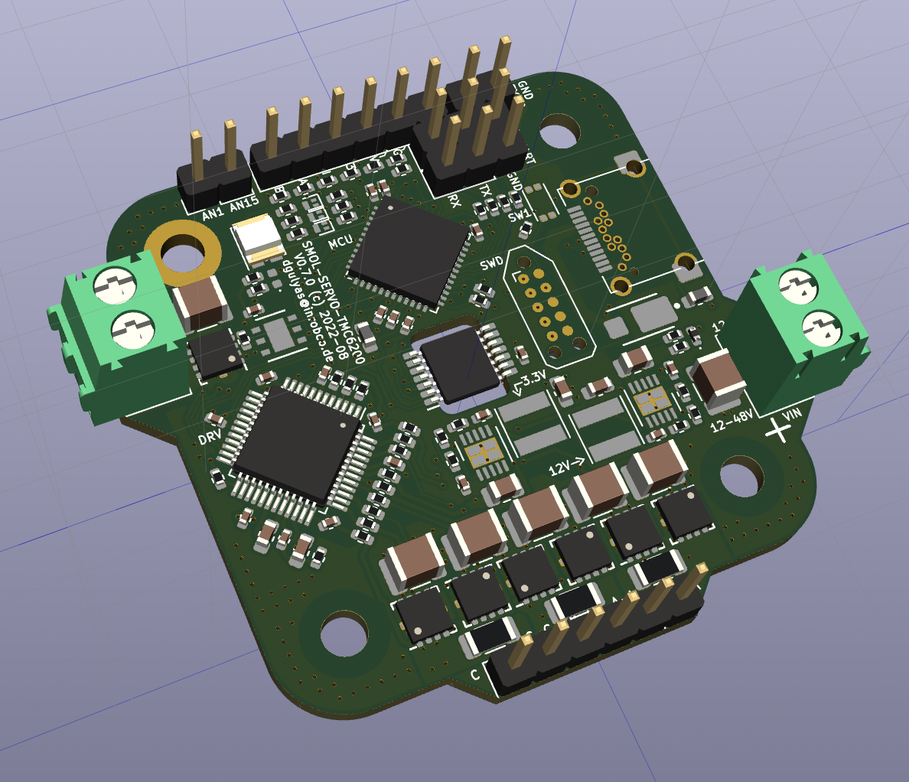
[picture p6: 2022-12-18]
doc/v0.7.0-board-render.png

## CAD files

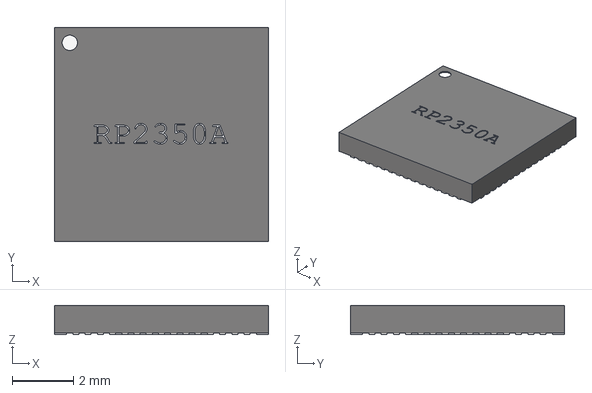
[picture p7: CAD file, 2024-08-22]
hardware/RP2350_QFN60.step
7.00 x 7.00 x 0.95 mm

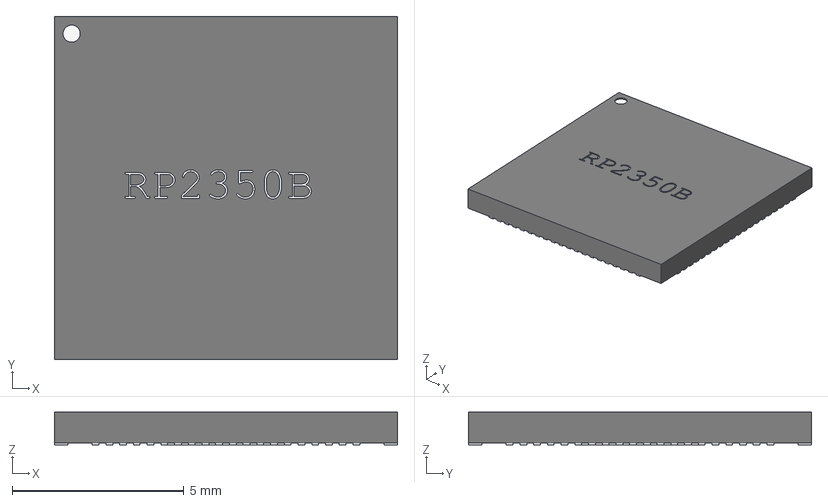
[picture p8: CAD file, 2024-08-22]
hardware/RP2350_QFN80.step
10.0 x 10.0 x 0.95 mm

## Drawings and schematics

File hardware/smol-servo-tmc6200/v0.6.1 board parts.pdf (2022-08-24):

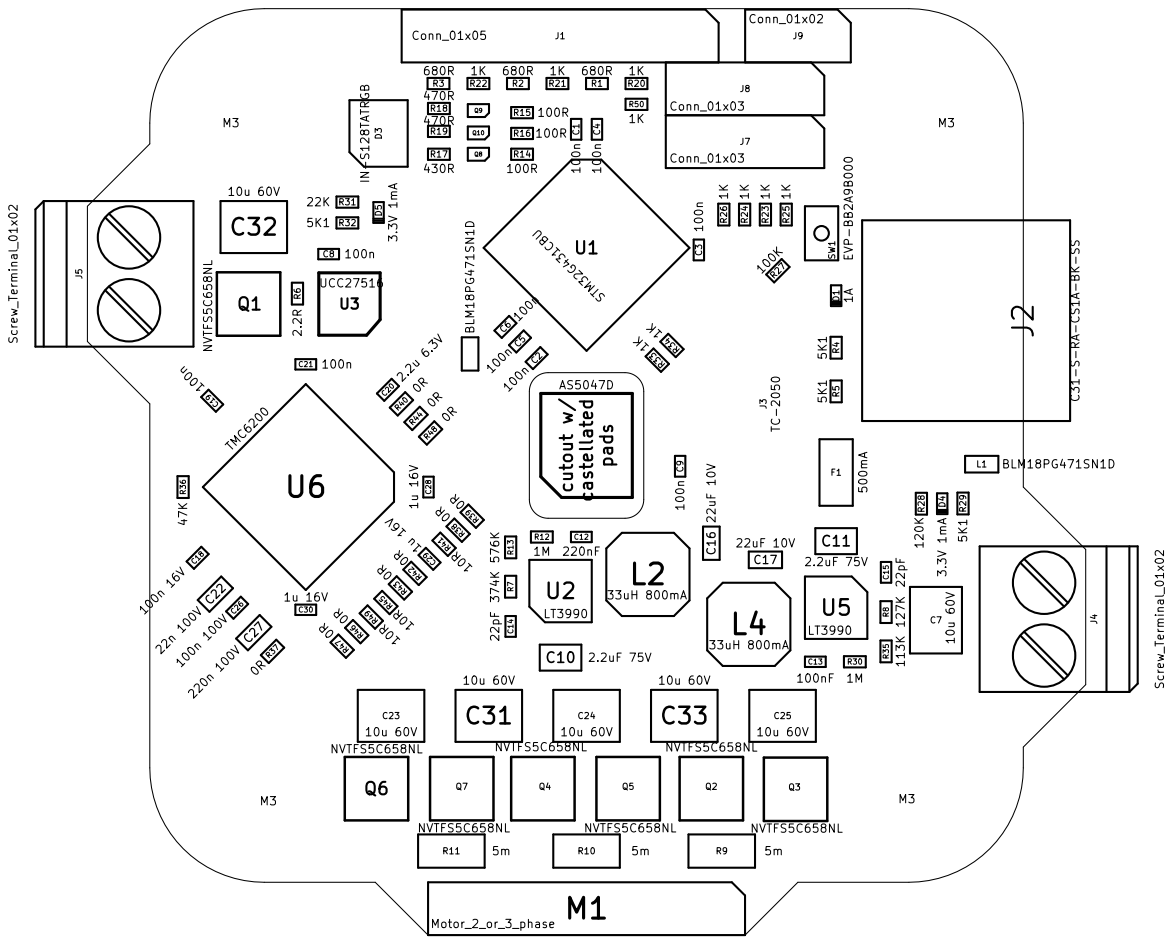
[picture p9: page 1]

C23 10u 60V | C31 NVTFS5C658NL | C24 10u 60V | C33 | C25 10u 60V

NVTFS5C658NL Q6 | Q7 | Q4 | Q5 | NVTFS5C658NL Q2 | Q3

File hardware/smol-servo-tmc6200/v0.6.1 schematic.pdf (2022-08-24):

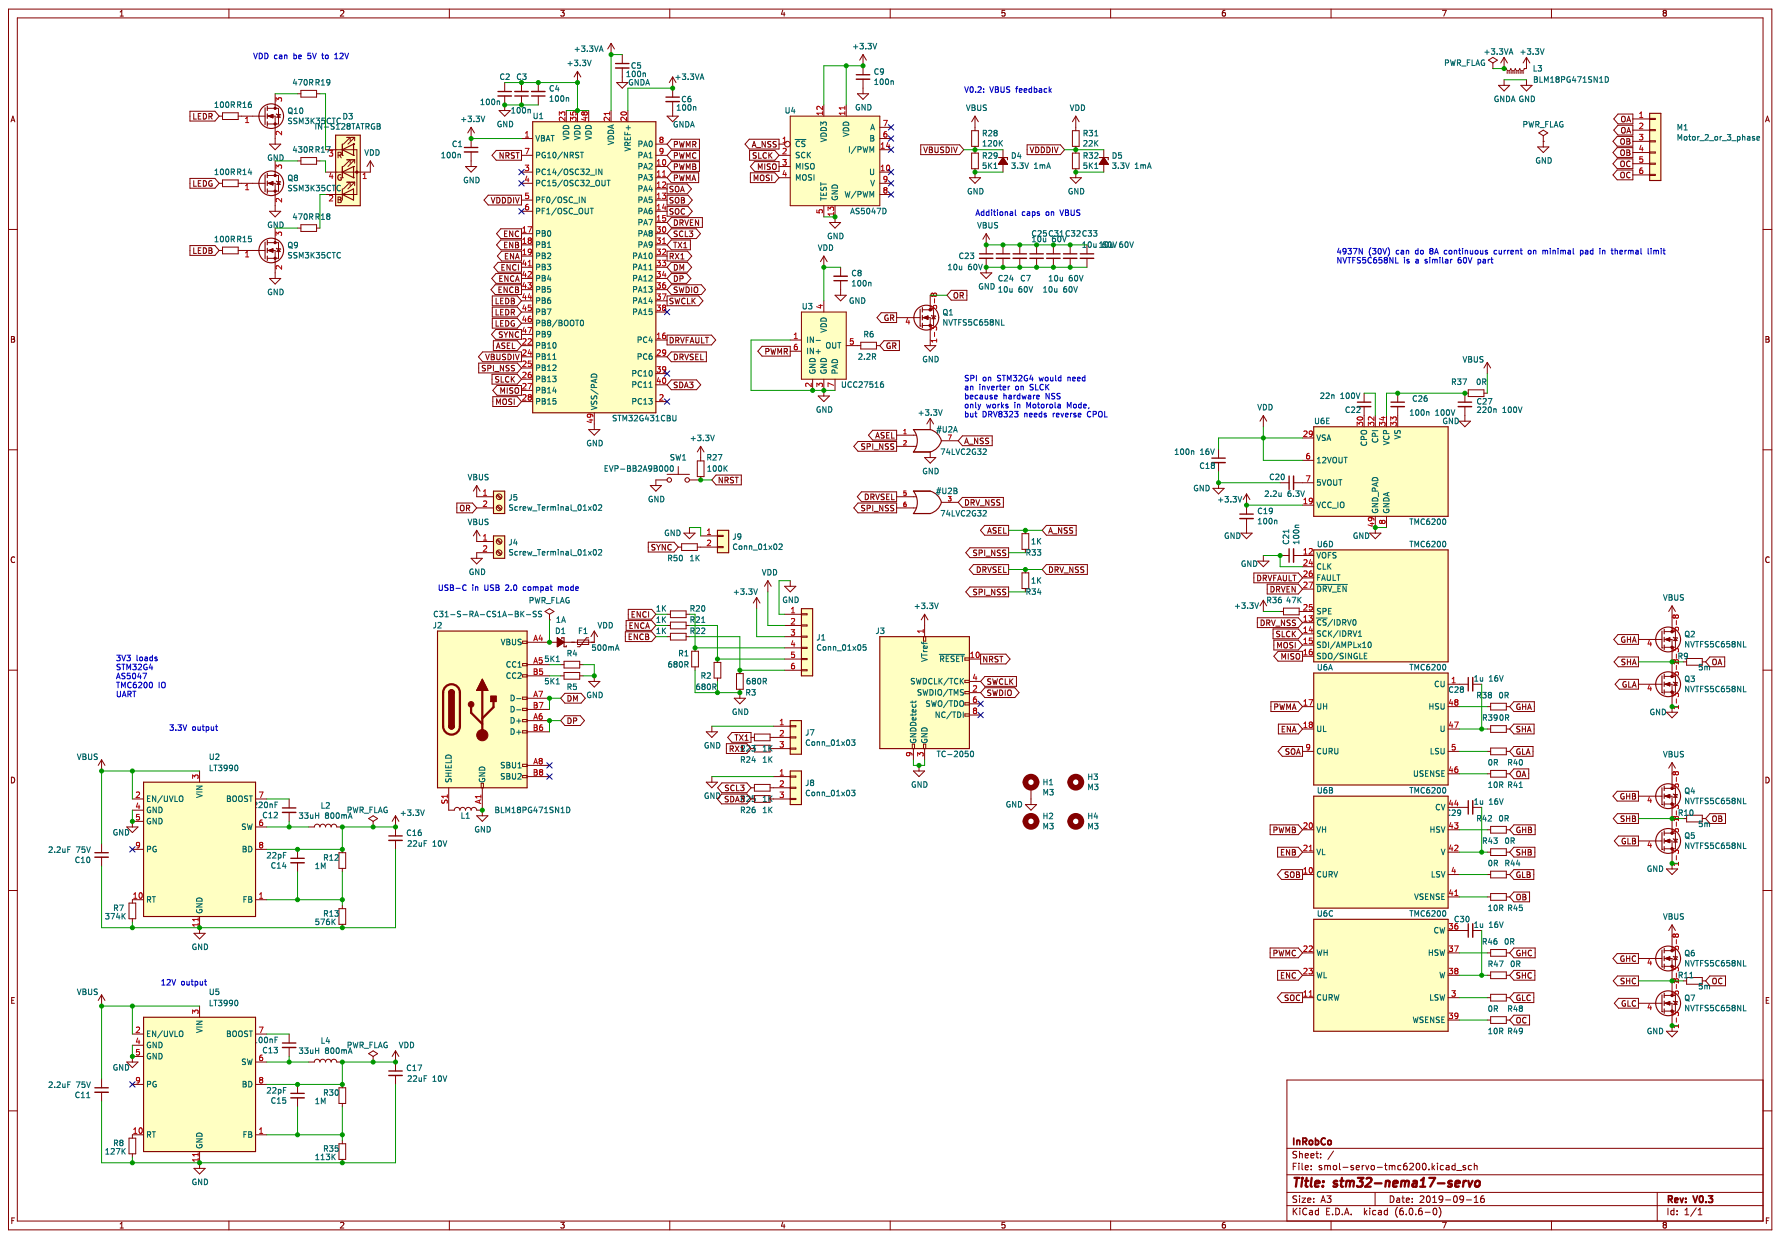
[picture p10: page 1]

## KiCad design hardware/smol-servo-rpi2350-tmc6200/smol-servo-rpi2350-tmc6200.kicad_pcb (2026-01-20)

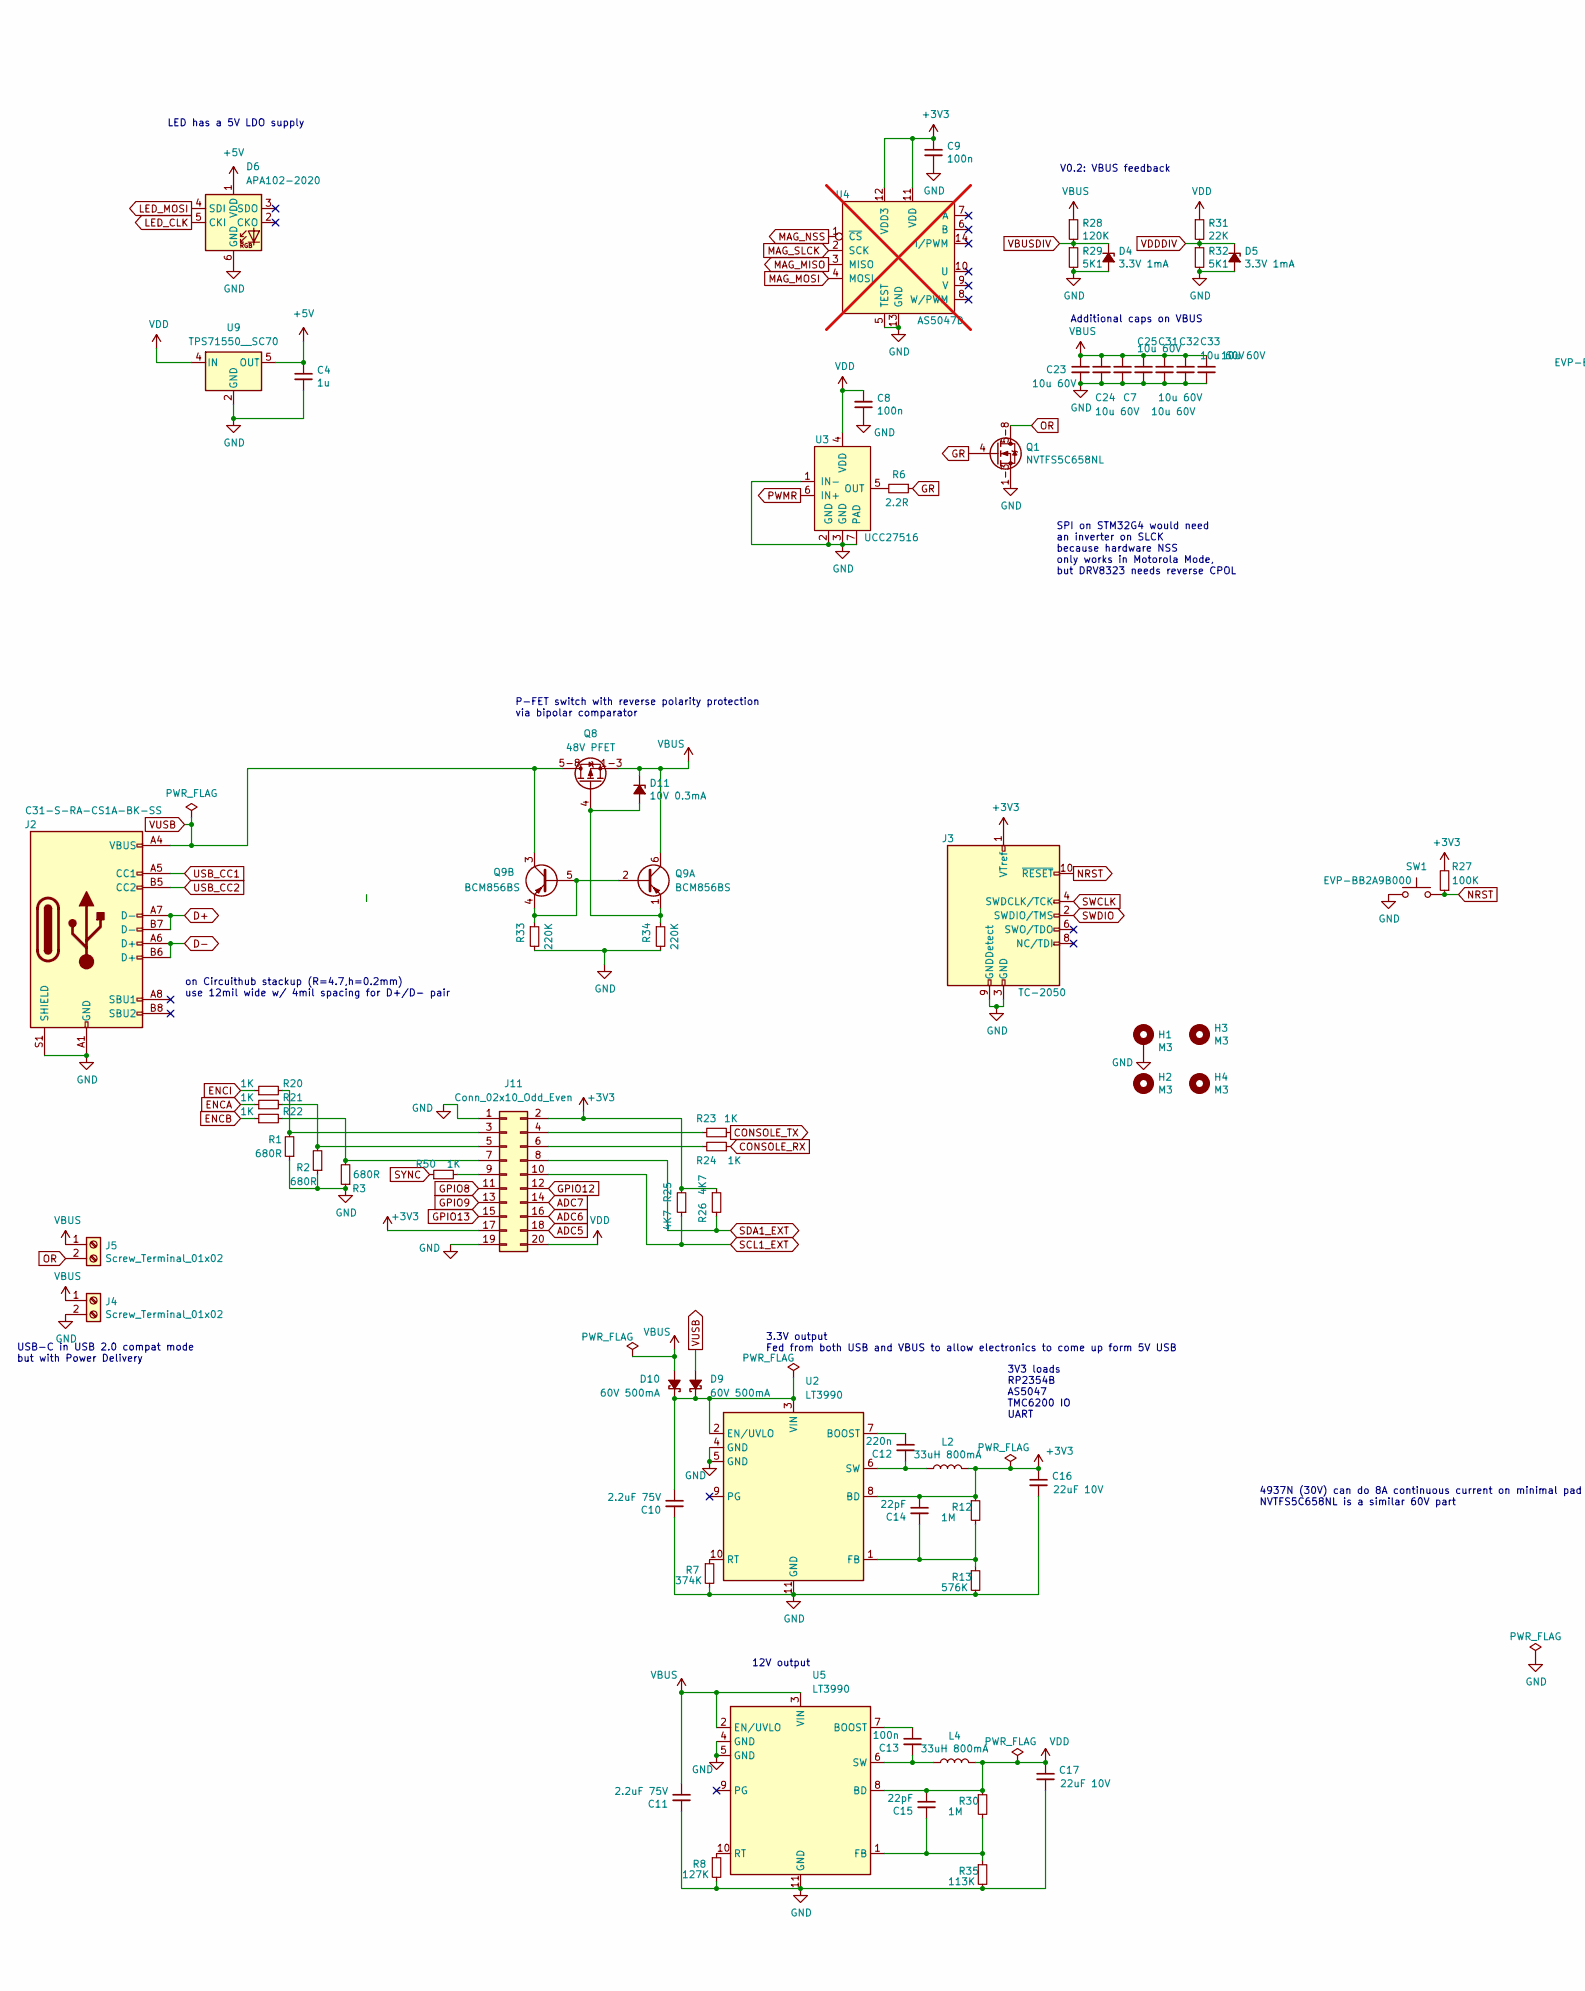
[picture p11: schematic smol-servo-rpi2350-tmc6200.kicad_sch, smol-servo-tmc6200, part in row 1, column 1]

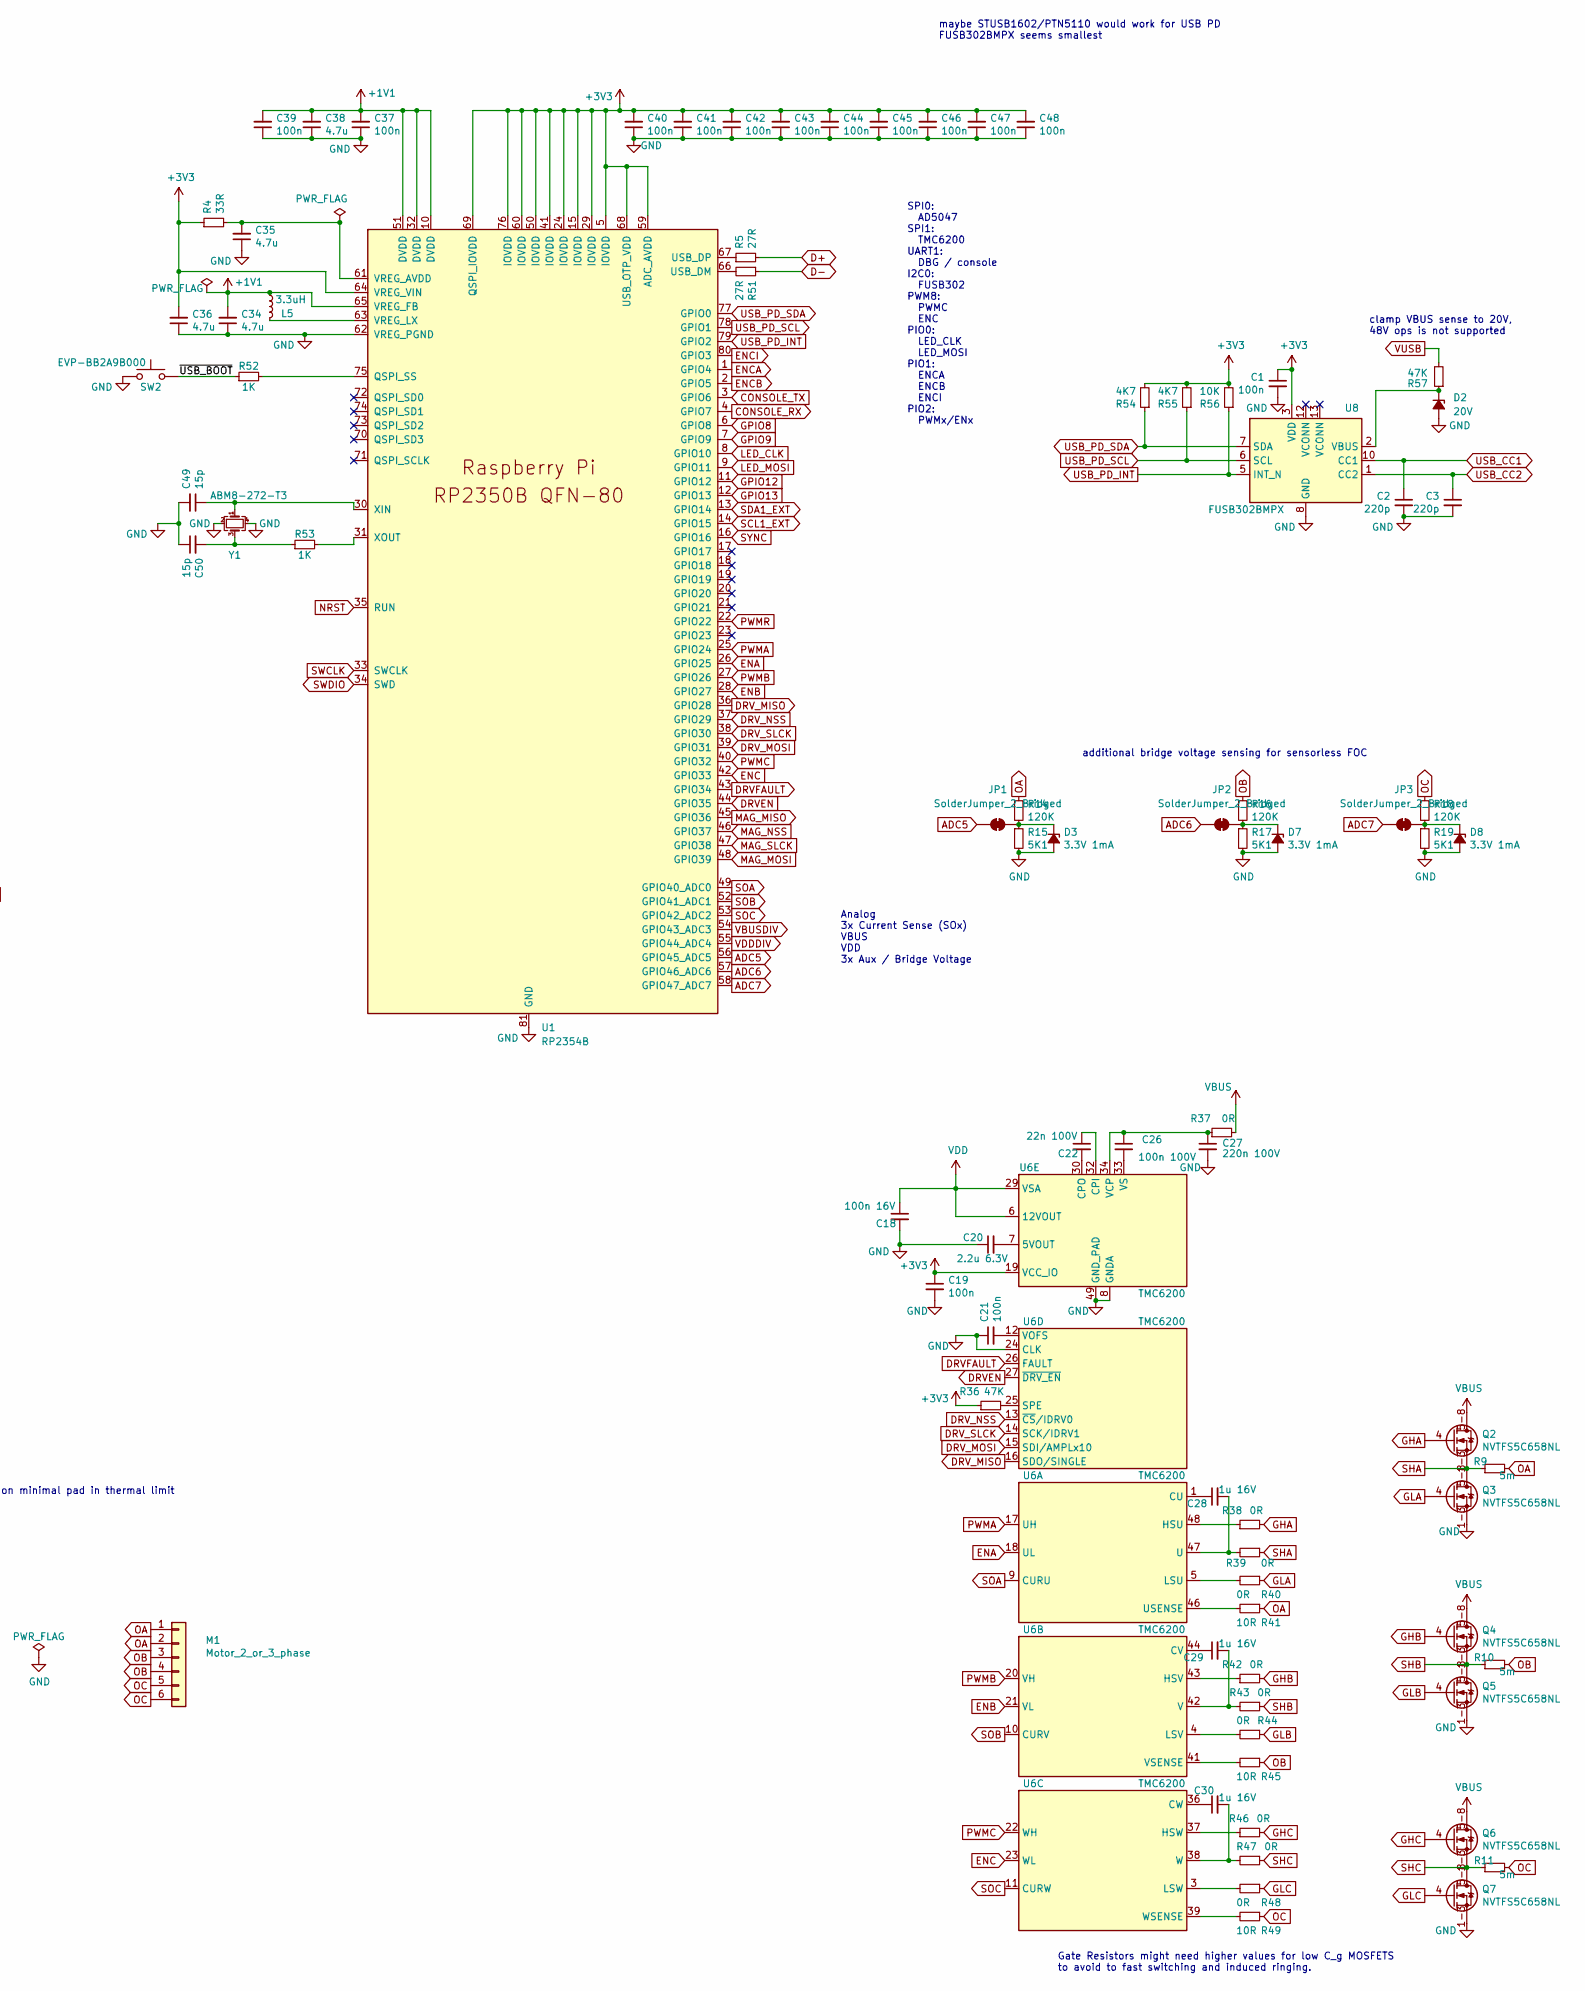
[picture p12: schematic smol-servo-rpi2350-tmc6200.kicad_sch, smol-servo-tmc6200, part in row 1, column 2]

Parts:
C1, C8, C9, C13, C19, C21, C37, C39, C40, C41, C42, C43, C44, C45, C46, C47, C48: 100n; C_0402_1005Metric; MPN CC0402KRX5R8BB104; JLCPCB C5137468
C2, C3: 220p; C_0402_1005Metric; MPN CC0402KRX5R8BB224; JLCPCB C39122
C4: 1u; C_0402_1005Metric; MPN CC0402KRX5R8BB105; JLCPCB C14445
C7, C23, C24, C25, C31, C32, C33: 10u 60V; C_1210_3225Metric; MPN C3225X7R1N106K250AC;CGA6P1X7R1N106M250AC; JLCPCB C5156756
C10, C11: 2.2uF 75V; C_0805_2012Metric; MPN GRM21BD72A225ME01K; JLCPCB C2981733
C12: 220n; C_0402_1005Metric; MPN CL05B224KO5NNNC; JLCPCB C16772
C14, C15: 22pF; C_0402_1005Metric; MPN CL05C220JB5NNNC; JLCPCB C1555
C16, C17: 22uF 10V; C_0603_1608Metric; MPN CM105X5R226M16AT;CL10A226MP8NUNE; JLCPCB C84419
C18: 100n 16V; C_0402_1005Metric; MPN CC0402KRX5R8BB104; JLCPCB C5137468
C20: 2.2u 6.3V; C_0402_1005Metric; MPN GRM155C80J225KE95D; JLCPCB C12530
C22: 22n 100V; C_0603_1608Metric; MPN C1608X7R2A223K080AA; JLCPCB C376821
C26: 100n 100V; C_0402_1005Metric; MPN GRM155R62A104ME14D; JLCPCB C162178
C27: 220n 100V; C_0603_1608Metric; MPN HMK107C7224KAHTE; JLCPCB C36911431
C28, C29, C30: 1u 16V; C_0402_1005Metric; MPN CL05A105KO5NNNC; JLCPCB C29266
C34, C35, C36, C38: 4.7u; C_0402_1005Metric; MPN CC0402MRX5R6BB475; JLCPCB C23733
C49, C50: 15p; C_0402_1005Metric; MPN CC0402JRNPO8BN150; JLCPCB C106997
D2: 20V; D_0603_1608Metric; MPN CZRU52C20;BZX584B20V; JLCPCB C968162
D3, D4, D5, D7, D8: 3.3V 1mA; D_0402_1005Metric; MPN CZRQR3V3B-HF; JLCPCB C3013401
D6: APA102-2020; LED-APA102-2020; MPN BB-2020BGR-TRB; JLCPCB C22439302
D9, D10: 60V 500mA; D_SOD-882; MPN PMEG6010ESBYL; JLCPCB C552935
D11: 10V 0.3mA; D_0402_1005Metric; MPN CZRQR10VB-HF;PZU10B2L,315; JLCPCB C553572
H1: M3; MountingHole_3.2mm_M3_DIN965_Pad
H2, H3, H4: M3; MountingHole_3.2mm_M3
J2: C31-S-RA-CS1A-BK-SS; USB_C_Receptacle_Adam_C31-S-RA-CS1X-BK; MPN C31-S-RA-CS1A-BK-SS;C31-S-RA-CS1E-BK-SS; JLCPCB C6582279
J3: TC-2050; Tag-Connect_TC2050-IDC-NL_2x05_P1.27mm_Vertical
J4, J5: Screw_Terminal_01x02; TerminalBlock_Phoenix_PT-1,5-2-3.5-H_1x02_P3.50mm_Horizontal
J11: Conn_02x10_Odd_Even; PinHeader_2x10_P1.00mm_Vertical
JP1, JP2, JP3: SolderJumper_2_Bridged; SolderJumper-2_P1.3mm_Bridged_RoundedPad1.0x1.5mm
L2, L4: 33uH 800mA; L_Taiyo-Yuden_NR-40xx; MPN TYS4030330M;MDWK4040T330MM; JLCPCB C2849475
L5: 3.3uH; L_pol_2016; MPN AOTA-B201610S3R3-101-T; JLCPCB C42411119
M1: Motor_2_or_3_phase; PinHeader_1x06_P2.54mm_Vertical
Q1, Q2, Q3, Q4, Q5, Q6, Q7: NVTFS5C658NL; WDFN8; MPN NVTFS5C658NL;NTTFS012N10MDTAG; JLCPCB C5208924
Q8: 48V PFET; WDFN8
Q9: BCM856BS; SOT-363_SC-70-6
R1, R2, R3: 680R; R_0402_1005Metric; MPN RC0402JR-07680RL; JLCPCB C25130
R4: 33R; R_0402_1005Metric; MPN RC0402FR-0733RL; JLCPCB C25105
R5, R51: 27R; R_0402_1005Metric; MPN RC0402FR-0727RL; JLCPCB C25100
R6: 2.2R; R_0402_1005Metric; MPN RC0402FR-072R2L; JLCPCB C25101
R7: 374K; R_0402_1005Metric; MPN RC0402FR-07374KL; JLCPCB C25781
R8: 127K; R_0402_1005Metric; MPN RC0402FR-07127KL; JLCPCB C11688
R9, R10, R11: 5m; R_1206_3216Metric; MPN PA1206FRF7W0R005L; JLCPCB C875584
R12, R30: 1M; R_0402_1005Metric; MPN RC0402FR-071ML; JLCPCB C26083
R13: 576K; R_0402_1005Metric; MPN RC0402FR-07576KL; JLCPCB C27012
R14, R16, R18, R28: 120K; R_0402_1005Metric; MPN RC0402FR-07120KL; JLCPCB C25750
R15, R17, R19, R29, R32: 5K1; R_0402_1005Metric; MPN RC0402FR-075K1L; JLCPCB C25905
R20, R21, R22, R23, R24, R50, R52, R53: 1K; R_0402_1005Metric; MPN RC0402FR-071KL; JLCPCB C11702
R25, R26, R54, R55: 4K7; R_0402_1005Metric; MPN RC0402FR-074K7L; JLCPCB C25900
R27: 100K; R_0402_1005Metric; MPN RC0402FR-07100KL; JLCPCB C25741
R31: 22K; R_0402_1005Metric; MPN RC0402FR-0722KL; JLCPCB C25768
R33, R34: 220K; R_0402_1005Metric; MPN RC0402FR-072R2L; JLCPCB C25767
R35: 113K; R_0402_1005Metric; MPN RC0402FR-07113KL; JLCPCB C25746
R36, R57: 47K; R_0402_1005Metric; MPN RC0402FR-0747KL; JLCPCB C25792
R37, R38, R39, R40, R42, R43, R44, R46, R47, R48: 0R; R_0402_1005Metric; MPN RC0402FR-070RL; JLCPCB C17168
R41, R45, R49: 10R; R_0402_1005Metric; MPN RC0402FR-0710RL; JLCPCB C102766
R56: 10K; R_0402_1005Metric; MPN RC0402FR-0710KL; JLCPCB C25744
SW1, SW2: EVP-BB2A9B000; SW_SPST_EVPBB; MPN EVP-BB2A9B000; JLCPCB C4365176
U1: RP2354B; RP2350-QFN-80-1EP_10x10_P0.4mm_EP3.4x3.4mm_ThermalVias; MPN RP2354B; JLCPCB C39843328
U2, U5: LT3990; DFN-10-1EP_3x3mm_P0.5mm_EP1.65x2.38mm_ThermalVias; MPN LT3990*DD; JLCPCB C580169
U3: UCC27516; Texas_PWSON-N6; MPN UCC27516; JLCPCB C3655221
U4: AS5047D; TSSOP-14_4.4x5mm_P0.65mm-inlaid; MPN AS5047D; not fitted
U6: TMC6200; TQFP-48-1EP_7x7mm_P0.5mm_EP5x5mm_ThermalVias; MPN TMC6200; JLCPCB C465958
U8: FUSB302BMPX; WQFN-14-1EP_2.5x2.5mm_P0.5mm_EP1.45x1.45mm; MPN FUSB302BMPX; JLCPCB C132291
U9: TPS71550__SC70; SOT-353_SC-70-5; MPN TPS71550; JLCPCB C571193
Y1: ABM8-272-T3; Oscillator_SMD_Abracon_ASE-4Pin_3.2x2.5mm; MPN ABM8-272-T3; JLCPCB C20625731

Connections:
+1V1: C34.2, C37.2, C38.2, C39.2, L5.1, U1.10 (DVDD), U1.32 (DVDD), U1.51 (DVDD), U1.65 (VREG_FB)
+3V3: C1.1, C9.1, C14.1, C16.1, C19.1, C36.2, C40.2, C41.2, C42.2, C43.2, C44.2, C45.2, C46.2, C47.2, C48.2, J3.1 (VTref), J11.2, J11.17, L2.2, R4.1, R12.1, R25.2, R26.1, R27.2, R36.1, R54.2, R55.2, R56.2, U1.5 (IOVDD), U1.15 (IOVDD), U1.24 (IOVDD), U1.29 (IOVDD), U1.41 (IOVDD), U1.50 (IOVDD), U1.59 (ADC_AVDD), U1.60 (IOVDD), U1.64 (VREG_VIN), U1.68 (USB_OTP_VDD), U1.69 (QSPI_IOVDD), U1.76 (IOVDD), U2.8 (BD), U4.11 (VDD), U4.12 (VDD3), U6.19 (VCC_IO), U8.3 (VDD), U8.4 (VDD)
+5V: C4.1, D6.1 (VDD), U9.5 (OUT)
/~USB_BOOT: R52.1, SW2.2
ADC5: J11.18, JP1.1 (A), U1.56 (GPIO45_ADC5)
ADC6: J11.16, JP2.1 (A), U1.57 (GPIO46_ADC6)
ADC7: J11.14, JP3.1 (A), U1.58 (GPIO47_ADC7)
CONSOLE_RX: R24.1, U1.4 (GPIO7)
CONSOLE_TX: R23.1, U1.3 (GPIO6)
D+: J2.A7 (D-), J2.B7 (D-), R5.2
D-: J2.A6 (D+), J2.B6 (D+), R51.1
DRVEN: U1.44 (GPIO35), U6.27 (~DRV_EN)
DRVFAULT: U1.43 (GPIO34), U6.26 (FAULT)
DRV_MISO: U1.36 (GPIO28), U6.16 (SDO/SINGLE)
DRV_MOSI: U1.39 (GPIO31), U6.15 (SDI/AMPLx10)
DRV_NSS: U1.37 (GPIO29), U6.13 (~CS/IDRV0)
DRV_SLCK: U1.38 (GPIO30), U6.14 (SCK/IDRV1)
ENA: U1.26 (GPIO25), U6.18 (UL)
ENB: U1.28 (GPIO27), U6.21 (VL)
ENC: U1.42 (GPIO33), U6.23 (WL)
ENCA: R21.1, U1.1 (GPIO4)
ENCB: R22.1, U1.2 (GPIO5)
ENCI: R20.1, U1.80 (GPIO3)
GHA: Q2.4 (G), R38.2
GHB: Q4.4 (G), R42.2
GHC: Q6.4 (G), R46.2
GLA: Q3.4 (G), R40.1
GLB: Q5.4 (G), R44.1
GLC: Q7.4 (G), R48.1
GND: C1.2, C2.2, C3.2, C4.2, C7.2, C8.1, C9.2, C10.2, C11.2, C16.2, C17.2, C18.2, C19.2, C20.1, C21.1, C23.2, C24.2, C25.2, C27.2, C31.2, C32.2, C33.2, C34.1, C35.1, C36.1, C37.1, C38.1, C39.1, C40.1, C41.1, C42.1, C43.1, C44.1, C45.1, C46.1, C47.1, C48.1, C49.2, C50.1, D2.2 (A), D3.2 (A), D4.2 (A), D5.2 (A), D6.6 (GND), D7.2 (A), D8.2 (A), H1.1, J2.A1 (GND), J2.A12 (GND), J2.B1 (GND), J2.B12 (GND), J2.S1 (SHIELD), J3.3 (GND), J3.5 (GND), J3.9 (GNDDetect), J4.2, J11.1, J11.19, Q1.1-3 (S), Q3.1-3 (S), Q5.1-3 (S), Q7.1-3 (S), R1.1, R2.1, R3.1, R7.2, R8.2, R13.2, R15.2, R17.2, R19.2, R29.2, R32.2, R33.2, R34.2, R35.2, SW1.1, SW2.1, U1.62 (VREG_PGND), U1.81 (GND), U2.4 (GND), U2.5 (GND), U2.11 (GND), U3.1 (IN-), U3.2 (GND), U3.3 (GND), U3.7 (PAD), U4.5 (TEST), U4.13 (GND), U5.4 (GND), U5.5 (GND), U5.11 (GND), U6.8 (GNDA), U6.24 (CLK), U6.49 (GND_PAD), U8.8 (GND), U8.9 (GND), U8.15 (GND), U9.2 (GND), Y1.2, Y1.4
GPIO8: J11.11, U1.6 (GPIO8)
GPIO9: J11.13, U1.7 (GPIO9)
GPIO12: J11.12, U1.11 (GPIO12)
GPIO13: J11.15, U1.12 (GPIO13)
GR: Q1.4 (G), R6.1
LED_CLK: D6.5 (CKI), U1.8 (GPIO10)
LED_MOSI: D6.4 (SDI), U1.9 (GPIO11)
MAG_MISO: U1.45 (GPIO36), U4.3 (MISO)
MAG_MOSI: U1.48 (GPIO39), U4.4 (MOSI)
MAG_NSS: U1.46 (GPIO37), U4.1 (~CS)
MAG_SLCK: U1.47 (GPIO38), U4.2 (SCK)
NRST: J3.10 (~RESET), R27.1, SW1.2, U1.35 (RUN)
unnamed: C50.2, R53.1, Y1.3
unnamed: D2.1 (K), R57.1, U8.2 (VBUS)
unnamed: D3.1 (K), JP1.2 (B), R14.2, R15.1
unnamed: D7.1 (K), JP2.2 (B), R16.2, R17.1
unnamed: D8.1 (K), JP3.2 (B), R18.2, R19.1
unnamed: C10.1, D9.1 (K), D10.1 (K), U2.2 (EN/UVLO), U2.3 (VIN)
unnamed: D11.2 (A), Q8.4 (G), Q9.1 (E1), R34.1
unnamed: J11.3, R1.2, R20.2
unnamed: J11.4, R23.2
unnamed: J11.5, R2.2, R21.2
unnamed: J11.6, R24.2
unnamed: J11.7, R3.2, R22.2
unnamed: J11.9, R50.2
unnamed: Q9.2 (B1), Q9.4 (E2), Q9.5 (B2), R33.1
unnamed: R52.2, U1.75 (QSPI_SS)
unnamed: R51.2, U1.66 (USB_DM)
unnamed: R5.1, U1.67 (USB_DP)
unnamed: C35.2, R4.2, U1.61 (VREG_AVDD)
unnamed: L5.2, U1.63 (VREG_LX)
unnamed: C49.1, U1.30 (XIN), Y1.1
unnamed: R53.2, U1.31 (XOUT)
unnamed: C12.1, U2.7 (BOOST)
unnamed: C14.2, R12.2, R13.1, U2.1 (FB)
unnamed: R7.1, U2.10 (RT)
unnamed: C12.2, L2.1, U2.6 (SW)
unnamed: R6.2, U3.5 (OUT)
unnamed: C13.1, U5.7 (BOOST)
unnamed: C15.2, R30.2, R35.1, U5.1 (FB)
unnamed: R8.1, U5.10 (RT)
unnamed: C13.2, L4.1, U5.6 (SW)
unnamed: C28.1, U6.1 (CU)
unnamed: R38.1, U6.48 (HSU)
unnamed: R40.2, U6.5 (LSU)
unnamed: C28.2, R39.2, U6.47 (U)
unnamed: R41.2, U6.46 (USENSE)
unnamed: C29.1, U6.44 (CV)
unnamed: R42.1, U6.43 (HSV)
unnamed: R44.2, U6.4 (LSV)
unnamed: C29.2, R43.2, U6.42 (V)
unnamed: R45.2, U6.41 (VSENSE)
unnamed: C30.1, U6.36 (CW)
unnamed: R46.1, U6.37 (HSW)
unnamed: R48.2, U6.3 (LSW)
unnamed: C30.2, R47.2, U6.38 (W)
unnamed: R49.2, U6.39 (WSENSE)
unnamed: R36.2, U6.25 (SPE)
unnamed: C21.2, U6.12 (VOFS)
unnamed: C20.2, U6.7 (5VOUT)
unnamed: C22.1, U6.32 (CPI)
unnamed: C22.2, U6.30 (CPO)
unnamed: C26.1, C27.1, R37.1, U6.34 (VCP)
unnamed: C26.2, U6.33 (VS)
OA: M1.1, M1.2, R9.2, R14.1, R41.1
OB: M1.3, M1.4, R10.2, R16.1, R45.1
OC: M1.5, M1.6, R11.2, R18.1, R49.1
OR: J5.2, Q1.5-8 (D)
PWMA: U1.25 (GPIO24), U6.17 (UH)
PWMB: U1.27 (GPIO26), U6.20 (VH)
PWMC: U1.40 (GPIO32), U6.22 (WH)
PWMR: U1.22 (GPIO22), U3.6 (IN+)
SCL1_EXT: J11.10, R25.1, U1.14 (GPIO15)
SDA1_EXT: J11.8, R26.2, U1.13 (GPIO14)
SHA: Q2.1-3 (S), Q3.5-8 (D), R9.1, R39.1
SHB: Q4.1-3 (S), Q5.5-8 (D), R10.1, R43.1
SHC: Q6.1-3 (S), Q7.5-8 (D), R11.1, R47.1
SOA: U1.49 (GPIO40_ADC0), U6.9 (CURU)
SOB: U1.52 (GPIO41_ADC1), U6.10 (CURV)
SOC: U1.53 (GPIO42_ADC2), U6.11 (CURW)
SWCLK: J3.4 (SWDCLK/TCK), U1.33 (SWCLK)
SWDIO: J3.2 (SWDIO/TMS), U1.34 (SWD)
SYNC: R50.1, U1.16 (GPIO16)
USB_CC1: C2.1, J2.A5 (CC1), U8.10 (CC1), U8.11 (CC1)
USB_CC2: C3.1, J2.B5 (CC2), U8.1 (CC2), U8.14 (CC2)
USB_PD_INT: R56.1, U1.79 (GPIO2), U8.5 (INT_N)
USB_PD_SCL: R55.1, U1.78 (GPIO1), U8.6 (SCL)
USB_PD_SDA: R54.1, U1.77 (GPIO0), U8.7 (SDA)
VBUS: C7.1, C11.1, C23.1, C24.1, C25.1, C31.1, C32.1, C33.1, D10.2 (A), D11.1 (K), J4.1, J5.1, Q2.5-8 (D), Q4.5-8 (D), Q6.5-8 (D), Q8.1-3 (S), Q9.6 (C1), R28.1, R37.2, U5.2 (EN/UVLO), U5.3 (VIN)
VBUSDIV: D4.1 (K), R28.2, R29.1, U1.54 (GPIO43_ADC3)
VDD: C8.2, C15.1, C17.1, C18.1, J11.20, L4.2, R30.1, R31.1, U3.4 (VDD), U5.8 (BD), U6.6 (12VOUT), U6.29 (VSA), U9.4 (IN)
VDDDIV: D5.1 (K), R31.2, R32.1, U1.55 (GPIO44_ADC4)
VUSB: D9.2 (A), J2.A4 (VBUS), J2.A9 (VBUS), J2.B4 (VBUS), J2.B9 (VBUS), Q8.5-8 (D), Q9.3 (C2), R57.2

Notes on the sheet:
3.3V output Fed from both USB and VBUS to allow electronics to come up form 5V USB
Additional caps on VBUS
maybe STUSB1602/PTN5110 would work for USB PD FUSB302BMPX seems smallest
4937N (30V) can do 8A continuous current on minimal pad in thermal limit NVTFS5C658NL is a similar 60V part
12V output
P-FET switch with reverse polarity protection via bipolar comparator
3V3 loads RP2354B AS5047 TMC6200 IO UART
Analog 3x Current Sense (SOx) VBUS VDD 3x Aux / Bridge Voltage
SPI0: AD5047 SPI1: TMC6200 UART1: DBG / console I2C0: FUSB302 PWM8: PWMC ENC PIO0: LED_CLK LED_MOSI PIO1: ENCA ENCB ENCI PIO2: PWMx/ENx
Gate Resistors might need higher values for low C_g MOSFETS to avoid to fast switching and induced ringing.
V0.2: VBUS feedback
SPI on STM32G4 would need an inverter on SLCK because hardware NSS only works in Motorola Mode, but DRV8323 needs reverse CPOL
clamp VBUS sense to 20V, 48V ops is not supported
on Circuithub stackup (R=4.7,h=0.2mm) use 12mil wide w/ 4mil spacing for D+/D- pair
LED has a 5V LDO supply
additional bridge voltage sensing for sensorless FOC
USB-C in USB 2.0 compat mode but with Power Delivery

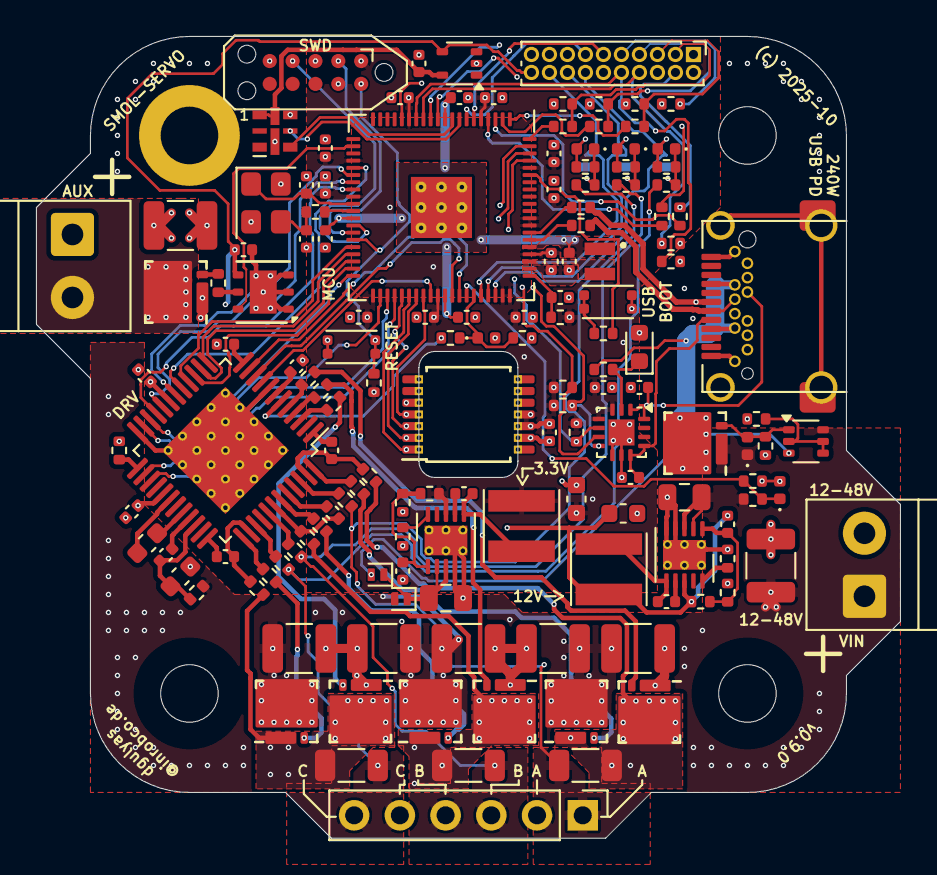
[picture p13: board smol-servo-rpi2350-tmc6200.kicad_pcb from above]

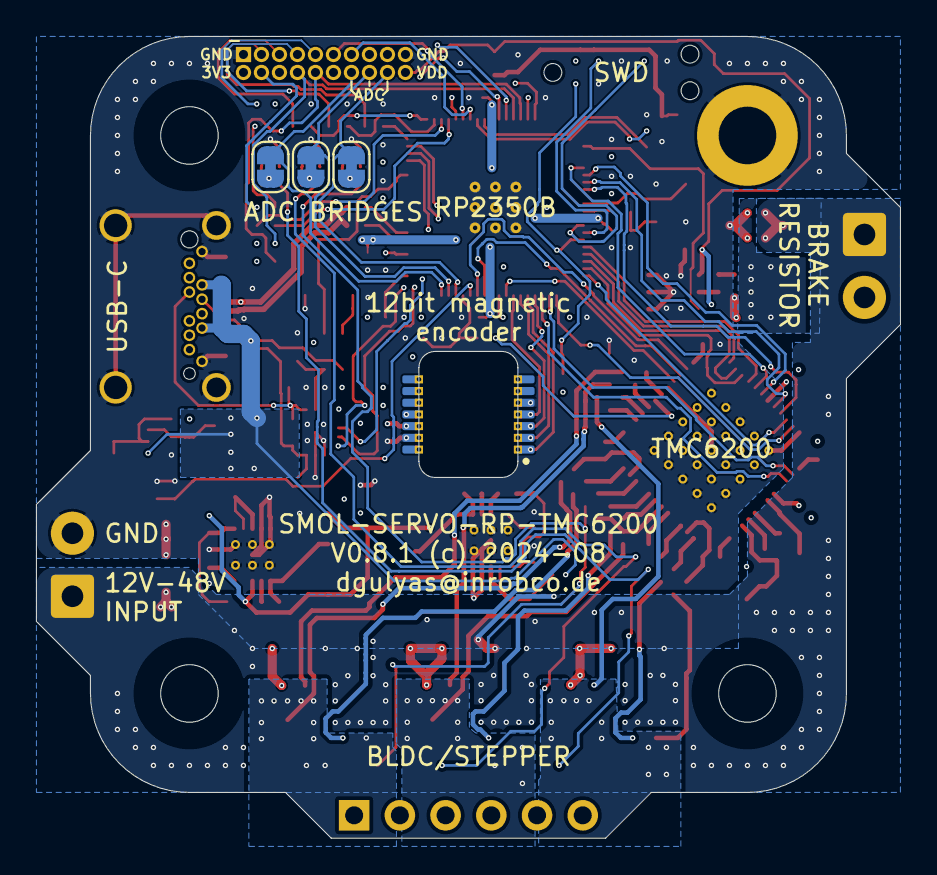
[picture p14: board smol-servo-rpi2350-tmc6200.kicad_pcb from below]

Board: 4 copper layers, 48.0 x 44.5 mm, 151 parts (3 on the bottom side), 123 nets.

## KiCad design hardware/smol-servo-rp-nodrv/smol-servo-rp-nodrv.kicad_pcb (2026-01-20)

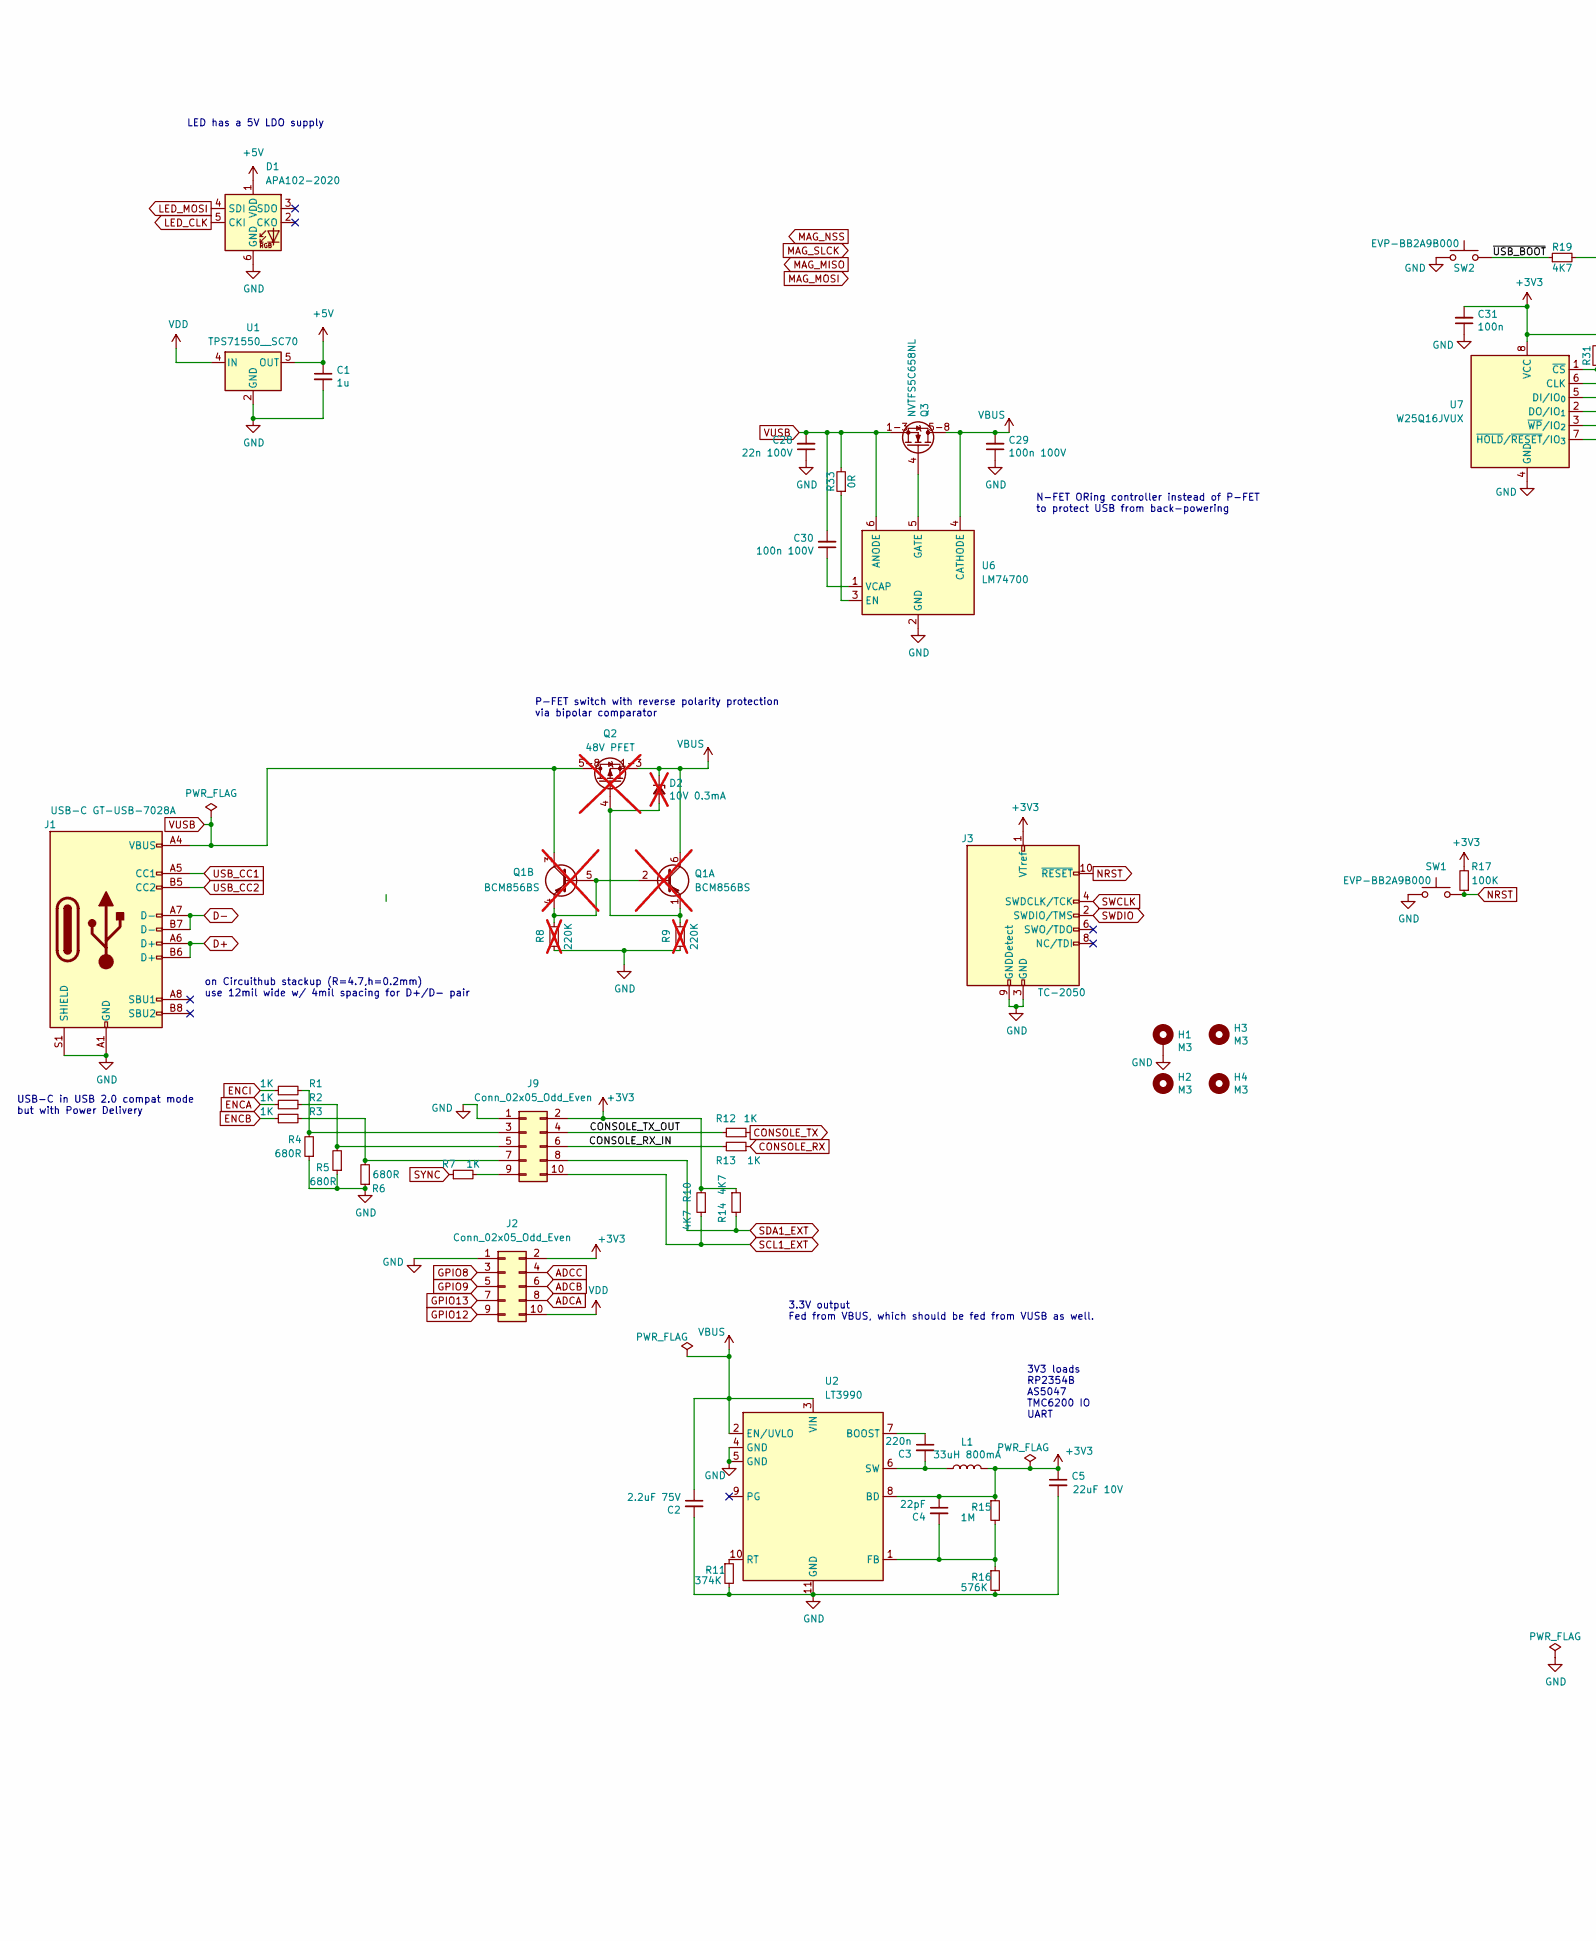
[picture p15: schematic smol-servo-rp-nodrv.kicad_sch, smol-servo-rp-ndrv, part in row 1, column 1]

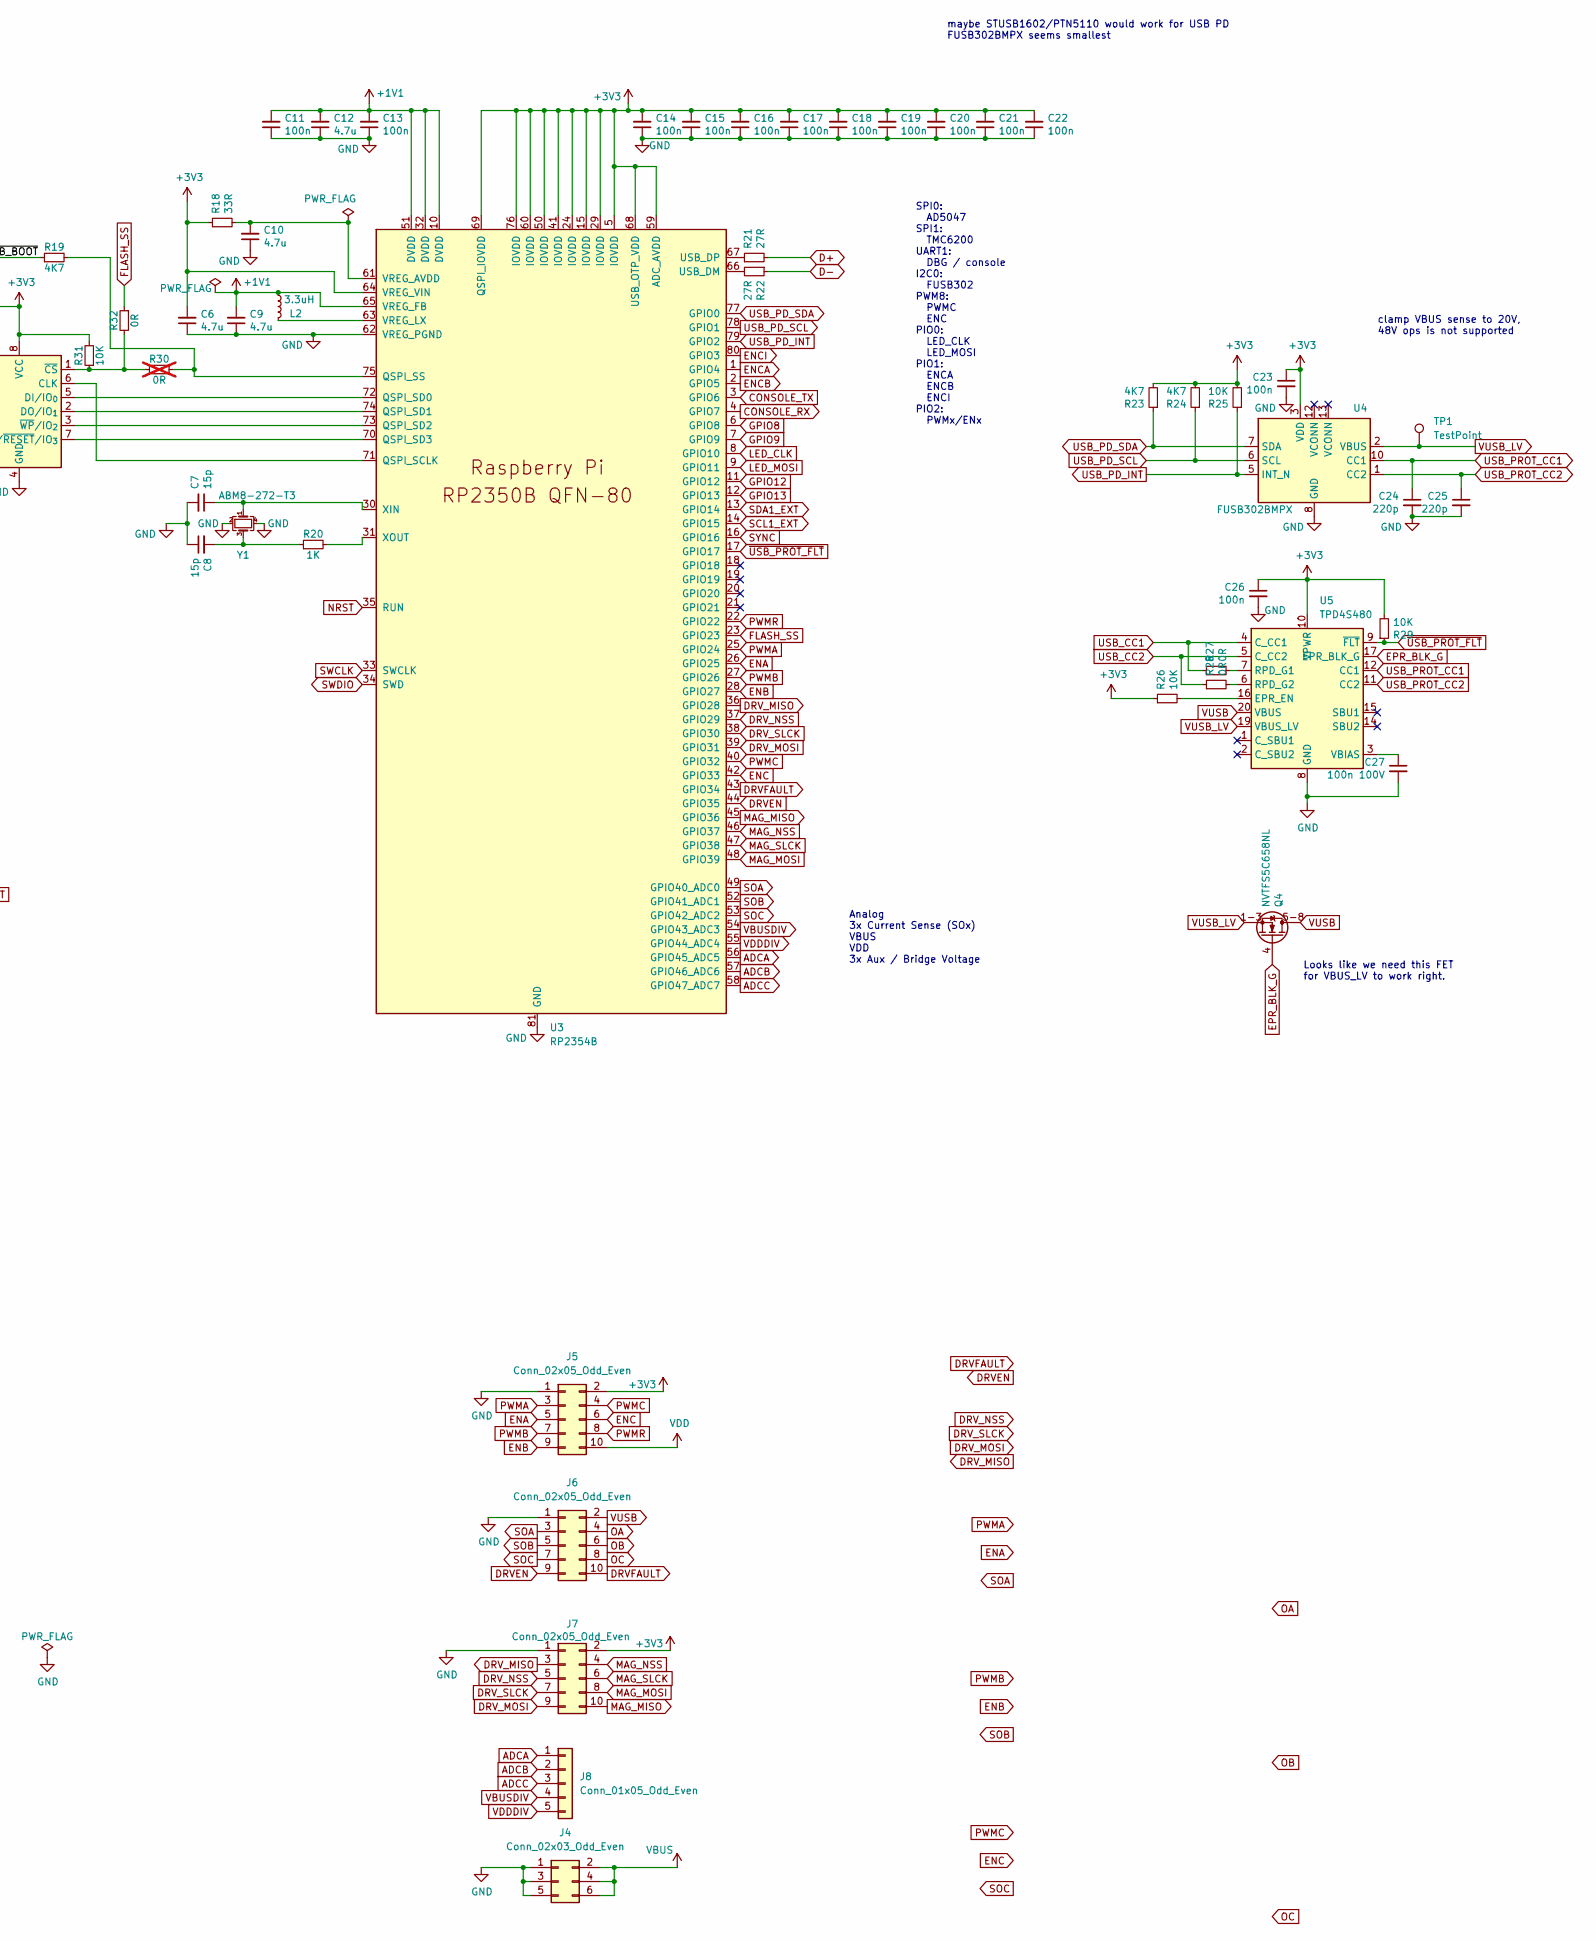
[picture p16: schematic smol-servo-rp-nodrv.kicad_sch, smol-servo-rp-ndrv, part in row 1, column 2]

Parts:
C1: 1u; C_0402_1005Metric; MPN CC0402KRX5R8BB105; JLCPCB C14445
C2: 2.2uF 75V; C_0805_2012Metric; MPN GRM21BD72A225ME01K; JLCPCB C2981733
C3: 220n; C_0402_1005Metric; MPN CL05B224KO5NNNC; JLCPCB C16772
C4: 22pF; C_0402_1005Metric; MPN CL05C220JB5NNNC; JLCPCB C1555
C5: 22uF 10V; C_0603_1608Metric; MPN CM105X5R226M16AT;CL10A226MP8NUNE; JLCPCB C84419
C6, C9, C10, C12: 4.7u; C_0402_1005Metric; MPN CC0402MRX5R6BB475; JLCPCB C23733
C7, C8: 15p; C_0402_1005Metric; MPN CC0402JRNPO8BN150; JLCPCB C106997
C11, C13, C14, C15, C16, C17, C18, C19, C20, C21, C22, C23, C26, C31: 100n; C_0402_1005Metric; MPN CC0402KRX5R8BB104; JLCPCB C5137468
C24, C25: 220p; C_0402_1005Metric; MPN CC0402KRX5R8BB224; JLCPCB C39122
C27, C29: 100n 100V; C_0402_1005Metric; MPN CC0402KRX5R8BB104; JLCPCB C5137468
C28: 22n 100V; C_0402_1005Metric; MPN GMC04X7R223K100NT; JLCPCB C3909603
C30: 100n 100V; C_0402_1005Metric; MPN GRM155R62A104KE14D; JLCPCB C162178
D1: APA102-2020; LED-APA102-2020; MPN BB-2020BGR-TRB; JLCPCB C22439302
D2: 10V 0.3mA; D_0402_1005Metric; MPN CZRQR10VB-HF;PZU10B2L,315; JLCPCB C553572; not fitted
H1: M3; MountingHole_3.2mm_M3_DIN965_Pad
H2, H3, H4: M3; MountingHole_3.2mm_M3
J1: USB-C GT-USB-7028A; USB_C_Receptacle_GT-USB-7028A; MPN GT-USB-7028A; JLCPCB C3001279
J2, J5, J6, J7, J9: Conn_02x05_Odd_Even; PinHeader_2x05_P2.54mm_Vertical
J3: TC-2050; Tag-Connect_TC2050-IDC-NL_2x05_P1.27mm_Vertical
J4: Conn_02x03_Odd_Even; PinHeader_2x03_P2.54mm_Vertical
J8: Conn_01x05_Odd_Even; PinHeader_1x05_P2.54mm_Vertical
L1: 33uH 800mA; L_Taiyo-Yuden_NR-40xx; MPN TYS4030330M;MDWK4040T330MM; JLCPCB C2849475
L2: 3.3uH; L_pol_2016; MPN AOTA-B201610S3R3-101-T; JLCPCB C42411119
Q1: BCM856BS; SOT-363_SC-70-6; not fitted
Q2: 48V PFET; WDFN8; not fitted
Q3, Q4: NVTFS5C658NL; WDFN8; MPN NVTFS5C658NL;NTTFS012N10MDTAG; JLCPCB C5208924
R1, R2, R3, R7, R12, R13, R20: 1K; R_0402_1005Metric; MPN RC0402FR-071KL; JLCPCB C11702
R4, R5, R6: 680R; R_0402_1005Metric; MPN RC0402JR-07680RL; JLCPCB C25130
R8, R9: 220K; R_0402_1005Metric; MPN RC0402FR-072R2L; JLCPCB C25767; not fitted
R10, R14, R23, R24: 4K7; R_0402_1005Metric; MPN RC0402FR-074K7L; JLCPCB C25900
R11: 374K; R_0402_1005Metric; MPN RC0402FR-07374KL; JLCPCB C25781
R15: 1M; R_0402_1005Metric; MPN RC0402FR-071ML; JLCPCB C26083
R16: 576K; R_0402_1005Metric; MPN RC0402FR-07576KL; JLCPCB C27012
R17: 100K; R_0402_1005Metric; MPN RC0402FR-07100KL; JLCPCB C25741
R18: 33R; R_0402_1005Metric; MPN RC0402FR-0733RL; JLCPCB C25105
R19: 4K7; R_0402_1005Metric; MPN RC0402FR-074K7L
R21, R22: 27R; R_0402_1005Metric; MPN RC0402FR-0727RL; JLCPCB C25100
R25, R26, R29: 10K; R_0402_1005Metric; MPN RC0402FR-0710KL; JLCPCB C25744
R27, R28, R32, R33: 0R; R_0402_1005Metric
R30: 0R; R_0402_1005Metric; not fitted
R31: 10K; R_0402_1005Metric; MPN RC0402FR-0710KL
SW1, SW2: EVP-BB2A9B000; SW_SPST_EVPBB; MPN EVP-BB2A9B000; JLCPCB C4365176
TP1: TestPoint; TestPoint_Pad_D1.0mm
U1: TPS71550__SC70; SOT-353_SC-70-5; MPN TPS71550; JLCPCB C571193
U2: LT3990; DFN-10-1EP_3x3mm_P0.5mm_EP1.65x2.38mm_ThermalVias; MPN LT3990*DD; JLCPCB C580169
U3: RP2354B; RP2350-QFN-80-1EP_10x10_P0.4mm_EP3.4x3.4mm_ThermalVias; MPN RP2354B; JLCPCB C39843328
U4: FUSB302BMPX; WQFN-14-1EP_2.5x2.5mm_P0.5mm_EP1.45x1.45mm; MPN FUSB302BMPX; JLCPCB C132291
U5: TPD4S480; WQFN-20-1EP_3x3mm_P0.4mm_EP1.7x1.7mm_ThermalVias
U6: LM74700; SOT-23-6
U7: W25Q16JVUX; Winbond_USON-8-1EP_3x2mm_P0.5mm_EP0.2x1.6mm
Y1: ABM8-272-T3; Oscillator_SMD_Abracon_ASE-4Pin_3.2x2.5mm; MPN ABM8-272-T3; JLCPCB C20625731

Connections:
+1V1: C9.2, C11.2, C12.2, C13.2, L2.1, U3.10 (DVDD), U3.32 (DVDD), U3.51 (DVDD), U3.65 (VREG_FB)
+3V3: C4.1, C5.1, C6.2, C14.2, C15.2, C16.2, C17.2, C18.2, C19.2, C20.2, C21.2, C22.2, C23.1, C26.1, C31.2, J2.2, J3.1 (VTref), J5.2, J7.2, J9.2, L1.2, R10.2, R14.1, R15.1, R17.2, R18.1, R23.2, R24.2, R25.2, R26.1, R29.2, R31.2, U2.8 (BD), U3.5 (IOVDD), U3.15 (IOVDD), U3.24 (IOVDD), U3.29 (IOVDD), U3.41 (IOVDD), U3.50 (IOVDD), U3.59 (ADC_AVDD), U3.60 (IOVDD), U3.64 (VREG_VIN), U3.68 (USB_OTP_VDD), U3.69 (QSPI_IOVDD), U3.76 (IOVDD), U4.3 (VDD), U4.4 (VDD), U5.10 (VPWR), U7.8 (VCC)
+5V: C1.1, D1.1 (VDD), U1.5 (OUT)
/CONSOLE_RX_IN: J9.6, R13.2
/CONSOLE_TX_OUT: J9.4, R12.2
/~USB_BOOT: R19.1, SW2.2
ADCA: J2.8, J8.1, U3.56 (GPIO45_ADC5)
ADCB: J2.6, J8.2, U3.57 (GPIO46_ADC6)
ADCC: J2.4, J8.3, U3.58 (GPIO47_ADC7)
CONSOLE_RX: R13.1, U3.4 (GPIO7)
CONSOLE_TX: R12.1, U3.3 (GPIO6)
D+: J1.A6 (D+), J1.B6 (D+), R21.2
D-: J1.A7 (D-), J1.B7 (D-), R22.1
DRVEN: J6.9, U3.44 (GPIO35)
DRVFAULT: J6.10, U3.43 (GPIO34)
DRV_MISO: J7.3, U3.36 (GPIO28)
DRV_MOSI: J7.9, U3.39 (GPIO31)
DRV_NSS: J7.5, U3.37 (GPIO29)
DRV_SLCK: J7.7, U3.38 (GPIO30)
ENA: J5.5, U3.26 (GPIO25)
ENB: J5.9, U3.28 (GPIO27)
ENC: J5.6, U3.42 (GPIO33)
ENCA: R2.1, U3.1 (GPIO4)
ENCB: R3.1, U3.2 (GPIO5)
ENCI: R1.1, U3.80 (GPIO3)
EPR_BLK_G: Q4.4 (G), U5.17 (EPR_BLK_G)
FLASH_SS: R32.1, U3.23 (GPIO23)
GND: C1.2, C2.2, C5.2, C6.1, C7.2, C8.1, C9.1, C10.1, C11.1, C12.1, C13.1, C14.1, C15.1, C16.1, C17.1, C18.1, C19.1, C20.1, C21.1, C22.1, C23.2, C24.2, C25.2, C26.2, C27.2, C28.1, C29.1, C31.1, D1.6 (GND), H1.1, J1.A1 (GND), J1.A12 (GND), J1.B1 (GND), J1.B12 (GND), J1.S1 (SHIELD), J2.1, J3.3 (GND), J3.5 (GND), J3.9 (GNDDetect), J4.1, J4.3, J4.5, J5.1, J6.1, J7.1, J9.1, R4.1, R5.1, R6.1, R8.2, R9.2, R11.2, R16.2, SW1.1, SW2.1, U1.2 (GND), U2.4 (GND), U2.5 (GND), U2.11 (GND), U3.62 (VREG_PGND), U3.81 (GND), U4.8 (GND), U4.9 (GND), U4.15 (GND), U5.8 (GND), U5.13 (GND), U5.18 (GND), U5.21 (GND), U6.2 (GND), U7.4 (GND), Y1.2, Y1.4
GPIO8: J2.3, U3.6 (GPIO8)
GPIO9: J2.5, U3.7 (GPIO9)
GPIO12: J2.9, U3.11 (GPIO12)
GPIO13: J2.7, U3.12 (GPIO13)
LED_CLK: D1.5 (CKI), U3.8 (GPIO10)
LED_MOSI: D1.4 (SDI), U3.9 (GPIO11)
MAG_MISO: J7.10, U3.45 (GPIO36)
MAG_MOSI: J7.8, U3.48 (GPIO39)
MAG_NSS: J7.4, U3.46 (GPIO37)
MAG_SLCK: J7.6, U3.47 (GPIO38)
NRST: J3.10 (~RESET), R17.1, SW1.2, U3.35 (RUN)
unnamed: C8.2, R20.1, Y1.3
unnamed: D2.2 (A), Q1.1 (E1), Q2.4 (G), R9.1
unnamed: J9.3, R1.2, R4.2
unnamed: J9.5, R2.2, R5.2
unnamed: J9.7, R3.2, R6.2
unnamed: J9.9, R7.2
unnamed: Q1.2 (B1), Q1.4 (E2), Q1.5 (B2), R8.1
unnamed: Q3.4 (G), U6.5 (GATE)
unnamed: C3.1, U2.7 (BOOST)
unnamed: C4.2, R15.2, R16.1, U2.1 (FB)
unnamed: R11.1, U2.10 (RT)
unnamed: C3.2, L1.1, U2.6 (SW)
unnamed: U3.71 (QSPI_SCLK), U7.6 (CLK)
unnamed: U3.72 (QSPI_SD0), U7.5 (DI/IO_{0})
unnamed: U3.74 (QSPI_SD1), U7.2 (DO/IO_{1})
unnamed: U3.73 (QSPI_SD2), U7.3 (~WP/IO_{2})
unnamed: U3.70 (QSPI_SD3), U7.7 (~HOLD/~RESET/IO_{3})
unnamed: R19.2, R30.2, U3.75 (QSPI_SS)
unnamed: R22.2, U3.66 (USB_DM)
unnamed: R21.1, U3.67 (USB_DP)
unnamed: C10.2, R18.2, U3.61 (VREG_AVDD)
unnamed: L2.2, U3.63 (VREG_LX)
unnamed: C7.1, U3.30 (XIN), Y1.1
unnamed: R20.2, U3.31 (XOUT)
unnamed: R26.2, U5.16 (EPR_EN)
unnamed: R27.2, U5.7 (RPD_G1)
unnamed: R28.2, U5.6 (RPD_G2)
unnamed: C27.1, U5.3 (VBIAS)
unnamed: R33.1, U6.3 (EN)
unnamed: C30.1, U6.1 (VCAP)
unnamed: R30.1, R31.1, R32.2, U7.1 (~CS)
OA: J6.4
OB: J6.6
OC: J6.8
PWMA: J5.3, U3.25 (GPIO24)
PWMB: J5.7, U3.27 (GPIO26)
PWMC: J5.4, U3.40 (GPIO32)
PWMR: J5.8, U3.22 (GPIO22)
SCL1_EXT: J9.10, R10.1, U3.14 (GPIO15)
SDA1_EXT: J9.8, R14.2, U3.13 (GPIO14)
SOA: J6.3, U3.49 (GPIO40_ADC0)
SOB: J6.5, U3.52 (GPIO41_ADC1)
SOC: J6.7, U3.53 (GPIO42_ADC2)
SWCLK: J3.4 (SWDCLK/TCK), U3.33 (SWCLK)
SWDIO: J3.2 (SWDIO/TMS), U3.34 (SWD)
SYNC: R7.1, U3.16 (GPIO16)
USB_CC1: J1.A5 (CC1), R27.1, U5.4 (C_CC1)
USB_CC2: J1.B5 (CC2), R28.1, U5.5 (C_CC2)
USB_PD_INT: R25.1, U3.79 (GPIO2), U4.5 (INT_N)
USB_PD_SCL: R24.1, U3.78 (GPIO1), U4.6 (SCL)
USB_PD_SDA: R23.1, U3.77 (GPIO0), U4.7 (SDA)
USB_PROT_CC1: C24.1, U4.10 (CC1), U4.11 (CC1), U5.12 (CC1)
USB_PROT_CC2: C25.1, U4.1 (CC2), U4.14 (CC2), U5.11 (CC2)
VBUS: C2.1, C29.2, D2.1 (K), J4.2, J4.4, J4.6, Q1.6 (C1), Q2.1-3 (S), Q3.5-8 (D), U2.2 (EN/UVLO), U2.3 (VIN), U6.4 (CATHODE)
VBUSDIV: J8.4, U3.54 (GPIO43_ADC3)
VDD: J2.10, J5.10, U1.4 (IN)
VDDDIV: J8.5, U3.55 (GPIO44_ADC4)
VUSB: C28.2, C30.2, J1.A4 (VBUS), J1.A9 (VBUS), J1.B4 (VBUS), J1.B9 (VBUS), J6.2, Q1.3 (C2), Q2.5-8 (D), Q3.1-3 (S), Q4.5-8 (D), R33.2, U5.20 (VBUS), U6.6 (ANODE)
VUSB_LV: Q4.1-3 (S), TP1.1, U4.2 (VBUS), U5.19 (VBUS_LV)
~USB_PROT_FLT: R29.1, U3.17 (GPIO17), U5.9 (~FLT)

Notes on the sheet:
3.3V output Fed from VBUS, which should be fed from VUSB as well.
Looks like we need this FET for VBUS_LV to work right.
maybe STUSB1602/PTN5110 would work for USB PD FUSB302BMPX seems smallest
P-FET switch with reverse polarity protection via bipolar comparator
3V3 loads RP2354B AS5047 TMC6200 IO UART
Analog 3x Current Sense (SOx) VBUS VDD 3x Aux / Bridge Voltage
SPI0: AD5047 SPI1: TMC6200 UART1: DBG / console I2C0: FUSB302 PWM8: PWMC ENC PIO0: LED_CLK LED_MOSI PIO1: ENCA ENCB ENCI PIO2: PWMx/ENx
clamp VBUS sense to 20V, 48V ops is not supported
N-FET ORing controller instead of P-FET to protect USB from back-powering
on Circuithub stackup (R=4.7,h=0.2mm) use 12mil wide w/ 4mil spacing for D+/D- pair
LED has a 5V LDO supply
USB-C in USB 2.0 compat mode but with Power Delivery

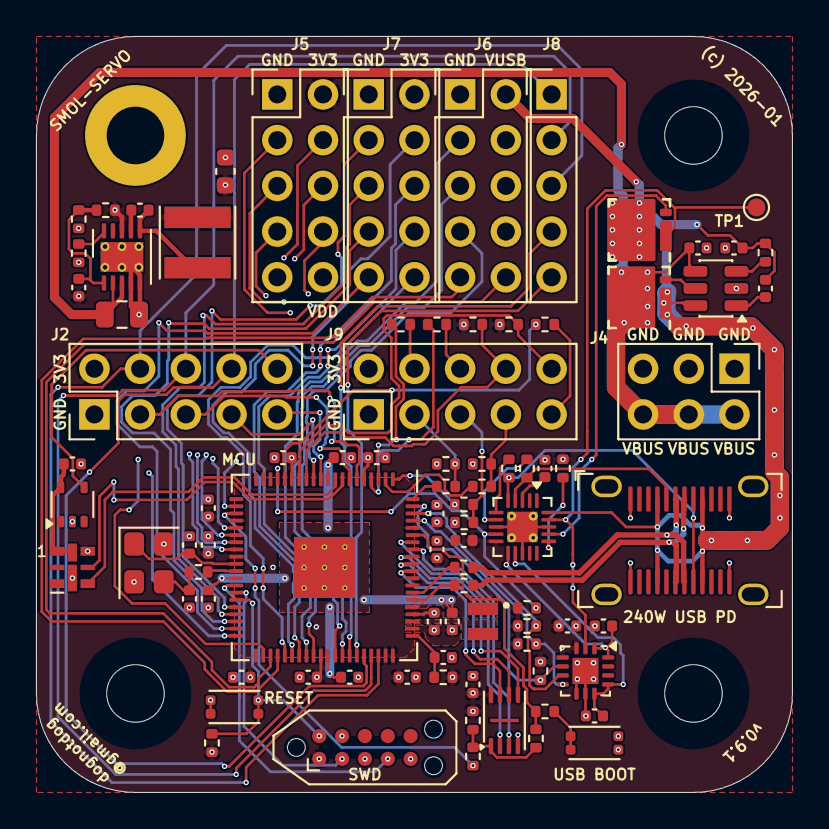
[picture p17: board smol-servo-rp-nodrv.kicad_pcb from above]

Board: 4 copper layers, 42.0 x 42.0 mm, 91 parts (0 on the bottom side), 94 nets.

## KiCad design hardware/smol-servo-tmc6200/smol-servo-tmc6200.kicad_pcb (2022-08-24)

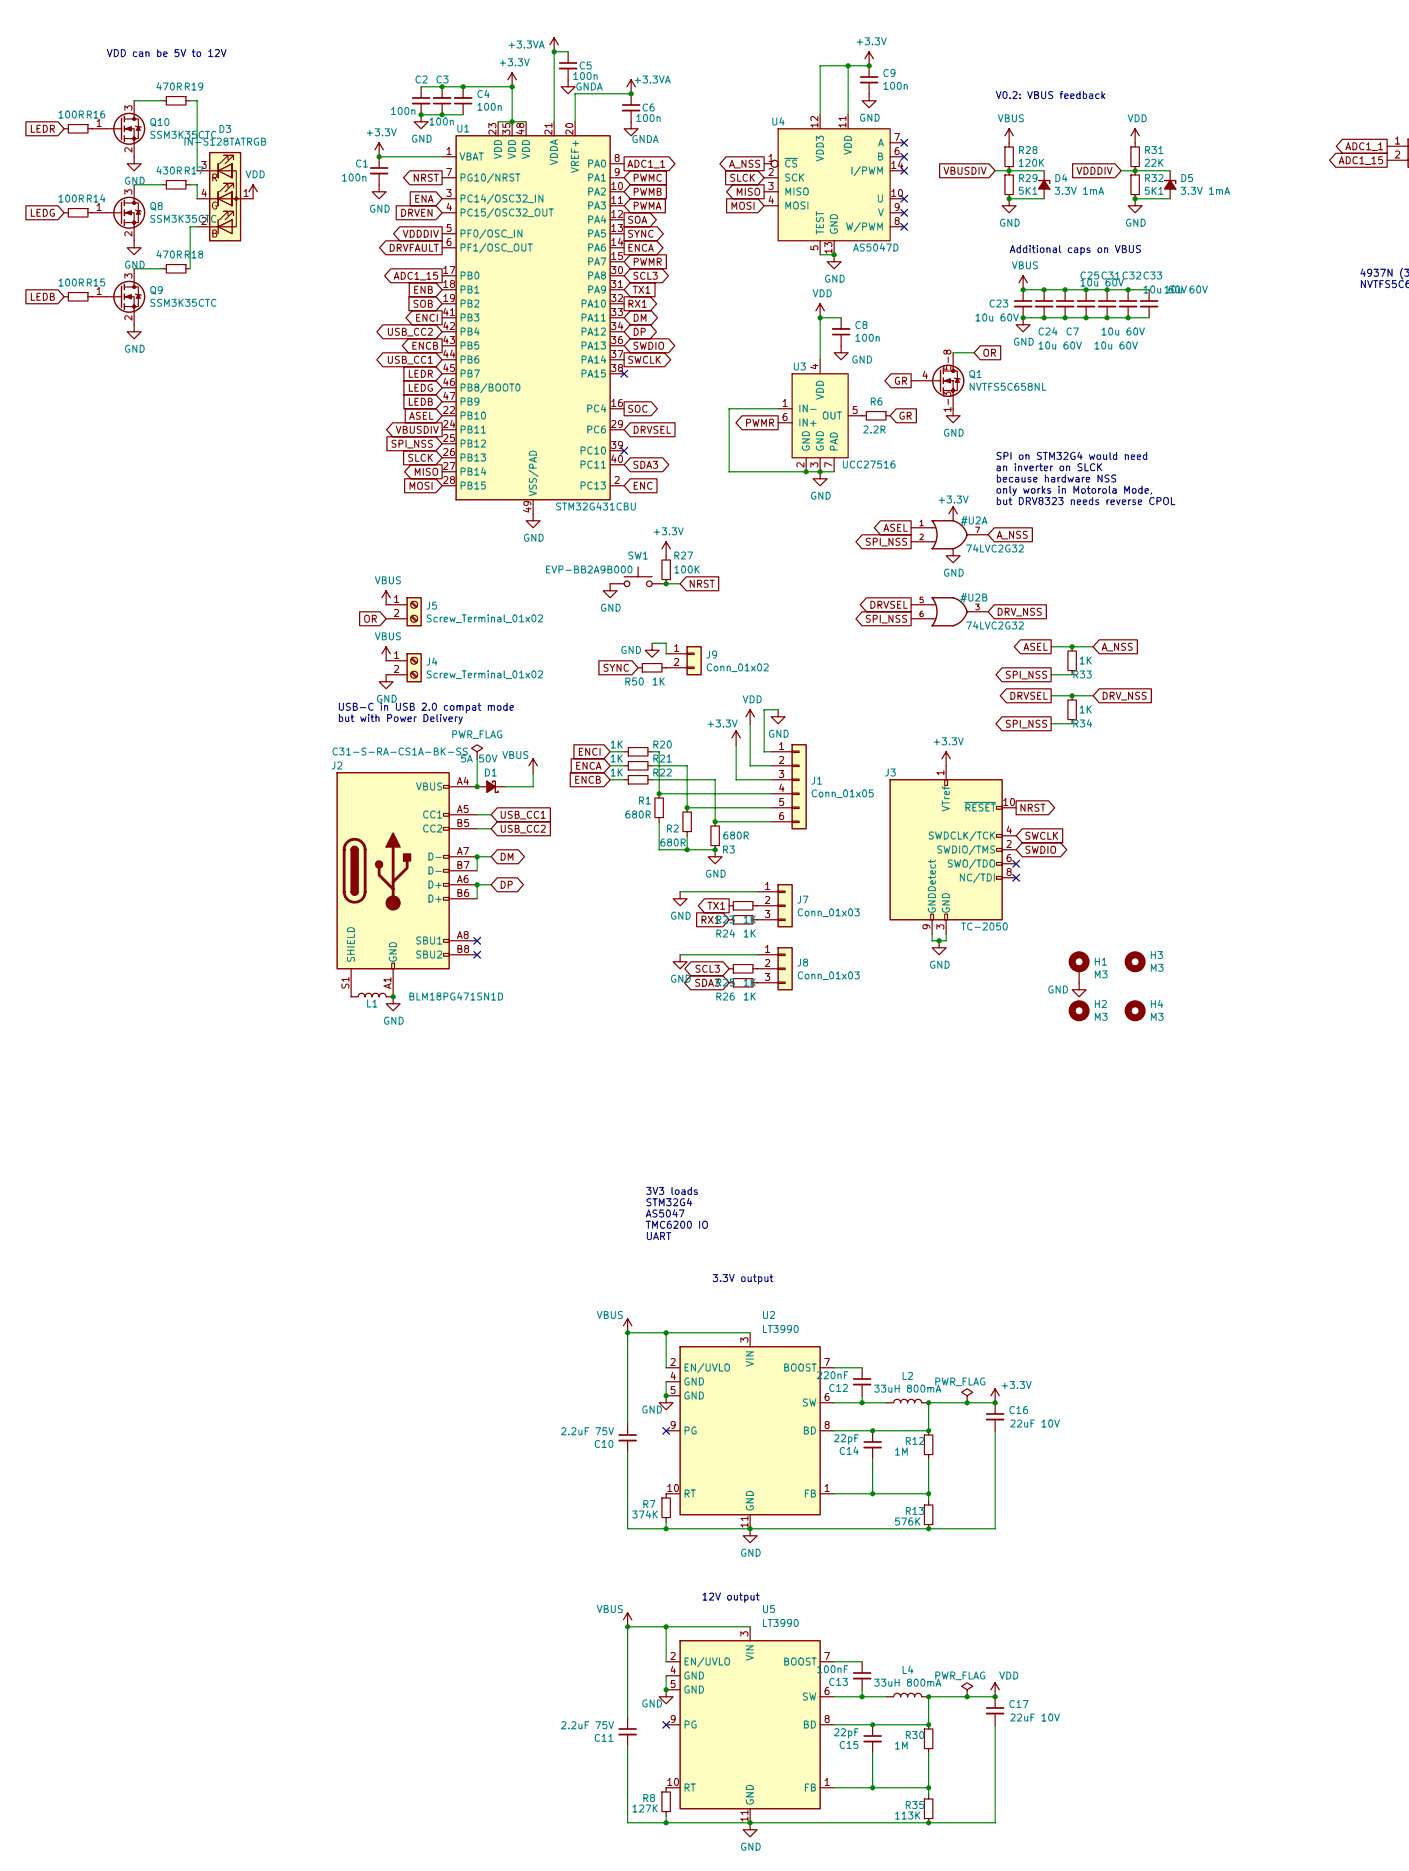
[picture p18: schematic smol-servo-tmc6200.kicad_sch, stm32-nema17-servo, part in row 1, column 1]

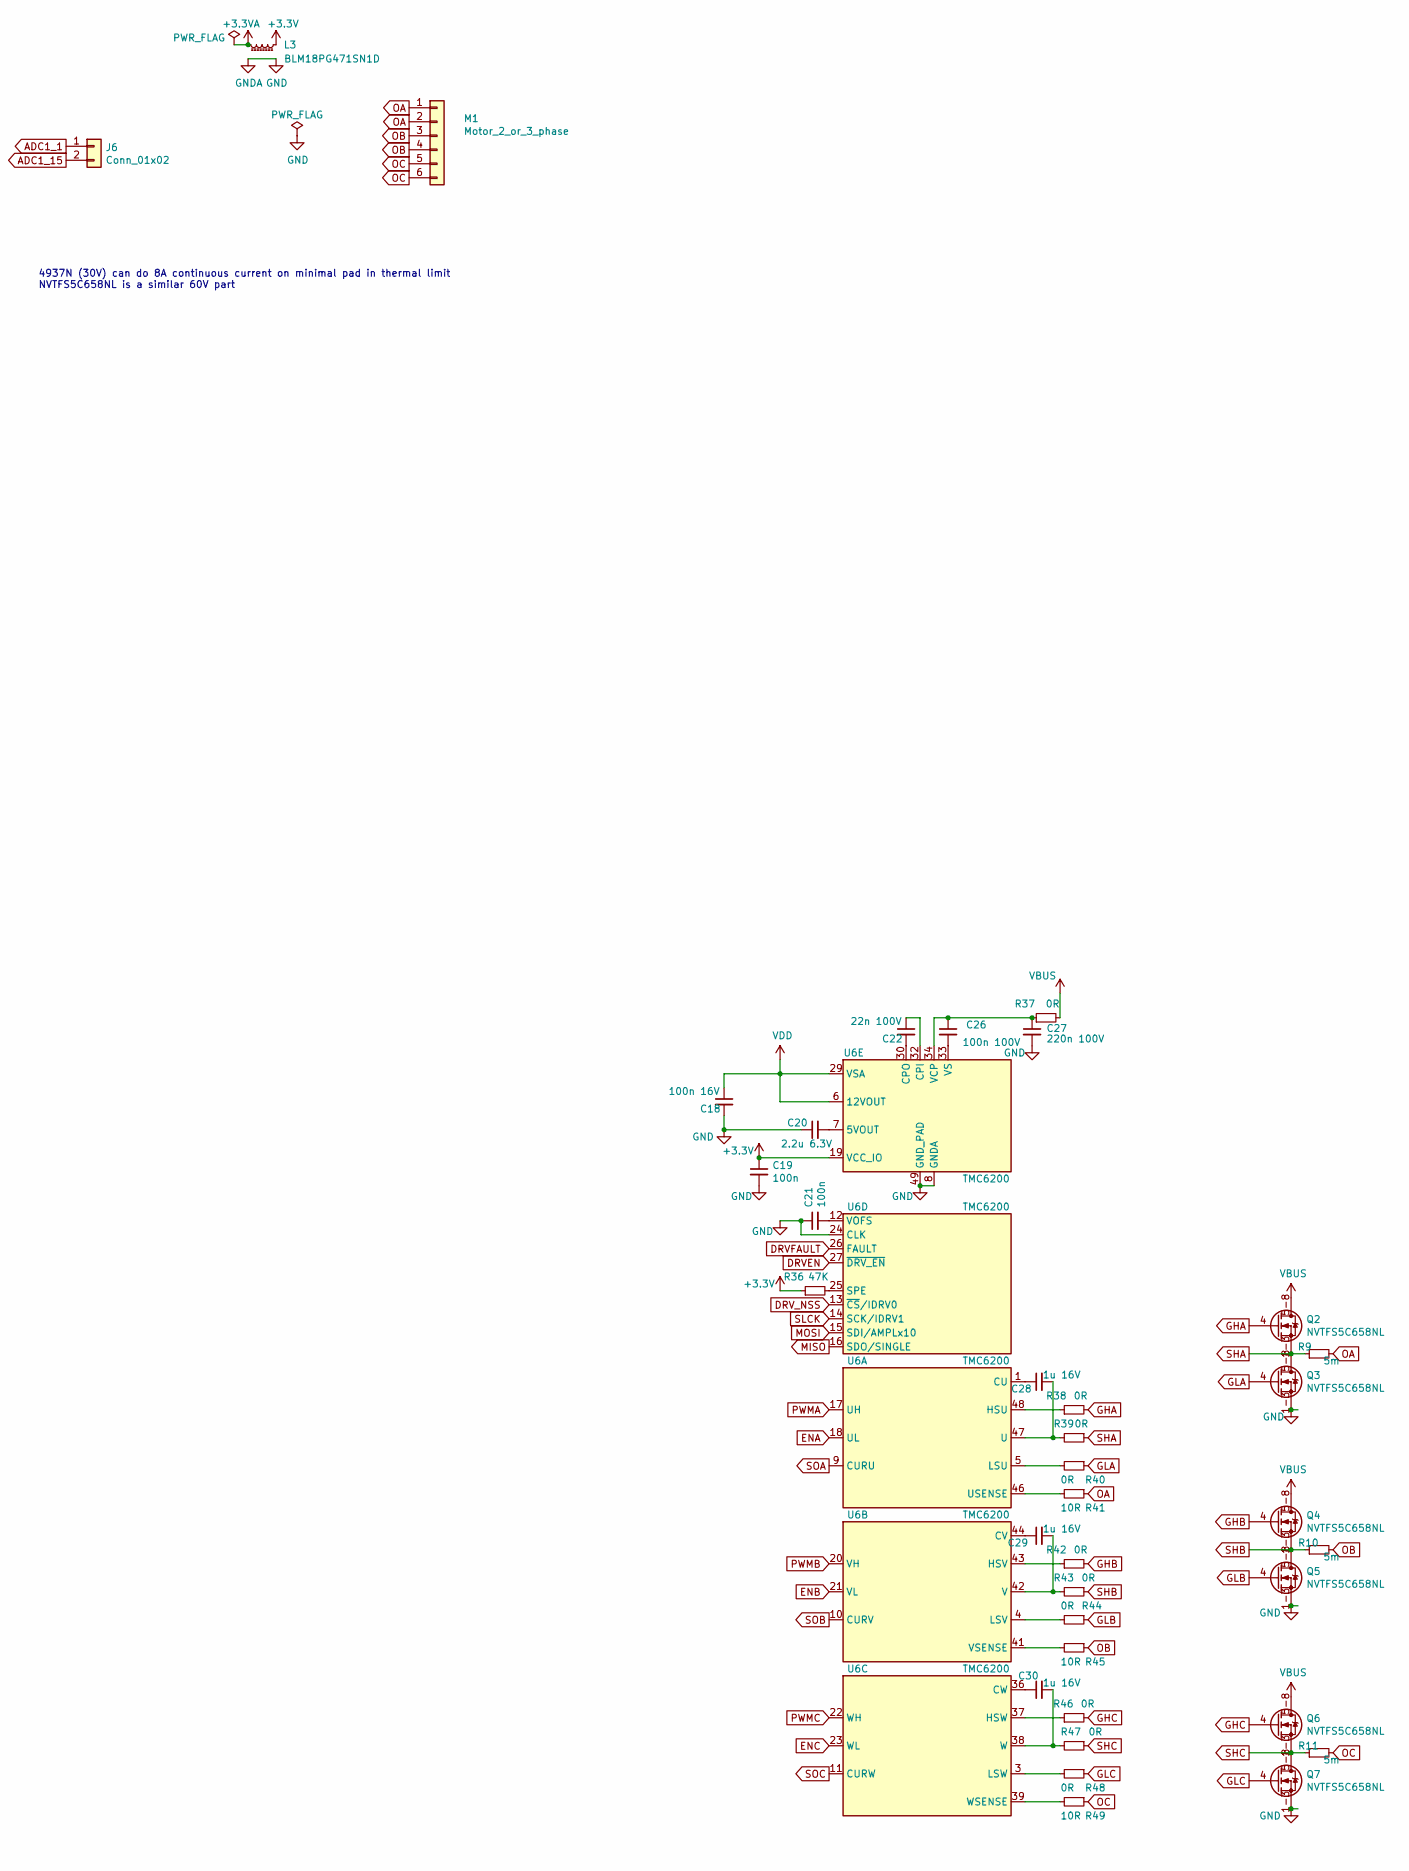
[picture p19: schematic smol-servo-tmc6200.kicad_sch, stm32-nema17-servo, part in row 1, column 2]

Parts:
C1, C2, C3, C4, C5, C6, C8, C9, C19, C21: 100n; C_0402_1005Metric; MPN CC0402KRX5R8BB104
C7, C23, C24, C25, C31, C32, C33: 10u 60V; C_1210_3225Metric; MPN C3225X7R1N106K250AC;CGA6P1X7R1N106M250AC
C10, C11: 2.2uF 75V; C_0805_2012Metric; MPN GRM21BD72A225ME01K
C12: 220nF; C_0402_1005Metric; MPN CL05B224KO5NNNC
C13: 100nF; C_0402_1005Metric; MPN CC0402KRX5R8BB104
C14, C15: 22pF; C_0402_1005Metric; MPN CL05C220JB5NNNC
C16, C17: 22uF 10V; C_0603_1608Metric; MPN CM105X5R226M16AT;CL10A226MP8NUNE
C18: 100n 16V; C_0402_1005Metric; MPN CC0402KRX5R8BB104
C20: 2.2u 6.3V; C_0402_1005Metric; MPN GRM155C80J225KE95D
C22: 22n 100V; C_0603_1608Metric; MPN C1608X7R2A223K080AA
C26: 100n 100V; C_0402_1005Metric; MPN GRM155R62A104ME14D
C27: 220n 100V; C_0603_1608Metric; MPN HMK107C7224KAHTE
C28, C29, C30: 1u 16V; C_0402_1005Metric; MPN CL05A105KO5NNNC
D1: 5A 50V; Diode-SMPA-DO-221BC; MPN V8PAM10S-M3/H
D3: IN-S128TATRGB; LED_Kingbright_AAA3528ESGCT; MPN IN-S128TATRGB
D4, D5: 3.3V 1mA; D_0402_1005Metric; MPN CZRQR3V3B-HF
H1: M3; MountingHole_3.2mm_M3_DIN965_Pad
H2, H3, H4: M3; MountingHole_3.2mm_M3
J1: Conn_01x05; PinHeader_1x06_P2.54mm_Vertical
J2: C31-S-RA-CS1A-BK-SS; USB_C_Receptacle_Adam_C31-S-RA-CS1X-BK; MPN C31-S-RA-CS1A-BK-SS;C31-S-RA-CS1E-BK-SS
J3: TC-2050; Tag-Connect_TC2050-IDC-NL_2x05_P1.27mm_Vertical
J4, J5: Screw_Terminal_01x02; TerminalBlock_Phoenix_PT-1,5-2-3.5-H_1x02_P3.50mm_Horizontal
J6, J9: Conn_01x02; PinHeader_1x02_P2.54mm_Vertical
J7, J8: Conn_01x03; PinHeader_1x03_P2.54mm_Vertical
L1, L3: BLM18PG471SN1D; L_0603_1608Metric; MPN BLM18PG471SN1D
L2, L4: 33uH 800mA; L_Taiyo-Yuden_NR-40xx; MPN TYS4030330M;MDWK4040T330MM
M1: Motor_2_or_3_phase; PinHeader_1x06_P2.54mm_Vertical
Q1, Q2, Q3, Q4, Q5, Q6, Q7: NVTFS5C658NL; WDFN8; MPN NVTFS5C658NL;NTTFS012N10MDTAG
Q8, Q9, Q10: SSM3K35CTC; SOT-883; MPN SSM3K35CTC
R1, R2, R3: 680R; R_0402_1005Metric; MPN RC0402JR-07680RL
R6: 2.2R; R_0402_1005Metric; MPN RC0402FR-072R2L
R7: 374K; R_0402_1005Metric; MPN RC0402FR-07374KL
R8: 127K; R_0402_1005Metric; MPN RC0402FR-07127KL
R9, R10, R11: 5m; R_1206_3216Metric; MPN PA1206FRF7W0R005L
R12, R30: 1M; R_0402_1005Metric; MPN RC0402FR-071ML
R13: 576K; R_0402_1005Metric; MPN RC0402FR-07576KL
R14, R15, R16: 100R; R_0402_1005Metric; MPN RC0402FR-07100RL
R17: 430R; R_0402_1005Metric; MPN RC0402FR-07430RL
R18, R19: 470R; R_0402_1005Metric; MPN RC0402FR-07470RL
R20, R21, R22, R23, R24, R25, R26, R33, R34, R50: 1K; R_0402_1005Metric; MPN RC0402FR-071KL
R27: 100K; R_0402_1005Metric; MPN RC0402FR-07100KL
R28: 120K; R_0402_1005Metric; MPN RC0402FR-07120KL
R29, R32: 5K1; R_0402_1005Metric; MPN RC0402FR-075K11L
R31: 22K; R_0402_1005Metric; MPN RC0402FR-0722KL
R35: 113K; R_0402_1005Metric; MPN RC0402FR-07113KL
R36: 47K; R_0402_1005Metric; MPN RC0402FR-0747KL
R37, R38, R39, R40, R42, R43, R44, R46, R47, R48: 0R; R_0402_1005Metric; MPN RC0402FR-070RL
R41, R45, R49: 10R; R_0402_1005Metric; MPN RC0402FR-0710RL
SW1: EVP-BB2A9B000; SW_SPST_EVPBB; MPN EVP-BB2A9B000
U1: STM32G431CBU; QFN-48-1EP_7x7mm_P0.5mm_EP5.6x5.6mm_ThermalVias; MPN STM32G431CBU
U2, U5: LT3990; DFN-10-1EP_3x3mm_P0.5mm_EP1.65x2.38mm_ThermalVias
U3: UCC27516; Texas_PWSON-N6; MPN UCC27516
U4: AS5047D; TSSOP-14_4.4x5mm_P0.65mm-inlaid; MPN AS5047D
U6: TMC6200; TQFP-48-1EP_7x7mm_P0.5mm_EP5x5mm_ThermalVias

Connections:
+3.3VA: C5.1, C6.1, L3.2, U1.20 (VREF+), U1.21 (VDDA)
ADC1_1: J6.1, U1.8 (PA0)
ADC1_15: J6.2, U1.17 (PB0)
DM: J2.A7 (D-), J2.B7 (D-), U1.33 (PA11)
DP: J2.A6 (D+), J2.B6 (D+), U1.34 (PA12)
DRVEN: U1.4 (PC15/OSC32_OUT), U6.27 (~DRV_EN)
DRVFAULT: U1.6 (PF1/OSC_OUT), U6.26 (FAULT)
ENA: U1.3 (PC14/OSC32_IN), U6.18 (UL)
ENB: U1.18 (PB1), U6.21 (VL)
ENC: U1.2 (PC13), U6.23 (WL)
ENCA: R21.1, U1.14 (PA6)
ENCB: R22.1, U1.43 (PB5)
ENCI: R20.1, U1.41 (PB3)
GHA: Q2.4 (G), R38.2
GHB: Q4.4 (G), R42.2
GHC: Q6.4 (G), R46.2
GLA: Q3.4 (G), R40.1
GLB: Q5.4 (G), R44.1
GLC: Q7.4 (G), R48.1
GR: Q1.4 (G), R6.1
LEDB: R15.2, U1.47 (PB9)
LEDG: R14.2, U1.46 (PB8/BOOT0)
LEDR: R16.2, U1.45 (PB7)
MISO: U1.27 (PB14), U4.3 (MISO), U6.16 (SDO/SINGLE)
MOSI: U1.28 (PB15), U4.4 (MOSI), U6.15 (SDI/AMPLx10)
NRST: J3.10 (~RESET), R27.1, SW1.2, U1.7 (PG10/NRST)
unnamed: C12.1, U2.7 (BOOST)
unnamed: C12.2, L2.1, U2.6 (SW)
unnamed: C13.1, U5.7 (BOOST)
unnamed: C13.2, L4.1, U5.6 (SW)
unnamed: C14.2, R12.2, R13.1, U2.1 (FB)
unnamed: C15.2, R30.2, R35.1, U5.1 (FB)
unnamed: C20.2, U6.7 (5VOUT)
unnamed: C21.2, U6.12 (VOFS)
unnamed: C22.1, U6.32 (CPI)
unnamed: C22.2, U6.30 (CPO)
unnamed: C26.1, C27.1, R37.1, U6.34 (VCP)
unnamed: C26.2, U6.33 (VS)
unnamed: C28.1, U6.1 (CU)
unnamed: C28.2, R39.2, U6.47 (U)
unnamed: C29.1, U6.44 (CV)
unnamed: C29.2, R43.2, U6.42 (V)
unnamed: C30.1, U6.36 (CW)
unnamed: C30.2, R47.2, U6.38 (W)
unnamed: D1.2 (A), J2.A4 (VBUS), J2.A9 (VBUS), J2.B4 (VBUS), J2.B9 (VBUS)
unnamed: D3.2 (BK), R18.1
unnamed: D3.3 (RK), R19.1
unnamed: D3.4 (GK), R17.1
unnamed: J1.4, R1.2, R20.2
unnamed: J1.5, R2.2, R21.2
unnamed: J1.6, R3.2, R22.2
unnamed: J2.S1 (SHIELD), L1.1
unnamed: J7.2, R23.2
unnamed: J7.3, R24.2
unnamed: J8.2, R25.2
unnamed: J8.3, R26.2
unnamed: J9.2, R50.2
unnamed: Q8.1 (G), R14.1
unnamed: Q8.3 (D), R17.2
unnamed: Q9.1 (G), R15.1
unnamed: Q9.3 (D), R18.2
unnamed: Q10.1 (G), R16.1
unnamed: Q10.3 (D), R19.2
unnamed: R6.2, U3.5 (OUT)
unnamed: R7.1, U2.10 (RT)
unnamed: R8.1, U5.10 (RT)
unnamed: R36.2, U6.25 (SPE)
unnamed: R38.1, U6.48 (HSU)
unnamed: R40.2, U6.5 (LSU)
unnamed: R41.2, U6.46 (USENSE)
unnamed: R42.1, U6.43 (HSV)
unnamed: R44.2, U6.4 (LSV)
unnamed: R45.2, U6.41 (VSENSE)
unnamed: R46.1, U6.37 (HSW)
unnamed: R48.2, U6.3 (LSW)
unnamed: R49.2, U6.39 (WSENSE)
OA: M1.1, M1.2, R9.2, R41.1
OB: M1.3, M1.4, R10.2, R45.1
OC: M1.5, M1.6, R11.2, R49.1
OR: J5.2, Q1.5-8 (D)
PWMA: U1.11 (PA3), U6.17 (UH)
PWMB: U1.10 (PA2), U6.20 (VH)
PWMC: U1.9 (PA1), U6.22 (WH)
PWMR: U1.15 (PA7), U3.6 (IN+)
RX1: R24.1, U1.32 (PA10)
SCL3: R25.1, U1.30 (PA8)
SDA3: R26.1, U1.40 (PC11)
SHA: Q2.1-3 (S), Q3.5-8 (D), R9.1, R39.1
SHB: Q4.1-3 (S), Q5.5-8 (D), R10.1, R43.1
SHC: Q6.1-3 (S), Q7.5-8 (D), R11.1, R47.1
SLCK: U1.26 (PB13), U4.2 (SCK), U6.14 (SCK/IDRV1)
SOA: U1.12 (PA4), U6.9 (CURU)
SOB: U1.19 (PB2), U6.10 (CURV)
SOC: U1.16 (PC4), U6.11 (CURW)
SWCLK: J3.4 (SWDCLK/TCK), U1.37 (PA14)
SWDIO: J3.2 (SWDIO/TMS), U1.36 (PA13)
SYNC: R50.1, U1.13 (PA5)
TX1: R23.1, U1.31 (PA9)
USB_CC1: J2.A5 (CC1), U1.44 (PB6)
USB_CC2: J2.B5 (CC2), U1.42 (PB4)
VBUS: C7.1, C10.1, C11.1, C23.1, C24.1, C25.1, C31.1, C32.1, C33.1, D1.1 (K), J4.1, J5.1, Q2.5-8 (D), Q4.5-8 (D), Q6.5-8 (D), R28.1, R37.2, U2.2 (EN/UVLO), U2.3 (VIN), U5.2 (EN/UVLO), U5.3 (VIN)
VBUSDIV: D4.1 (K), R28.2, R29.1, U1.24 (PB11)
VDD: C8.2, C15.1, C17.1, C18.1, D3.1 (A), J1.2, L4.2, R30.1, R31.1, U3.4 (VDD), U5.8 (BD), U6.6 (12VOUT), U6.29 (VSA)
VDDDIV: D5.1 (K), R31.2, R32.1, U1.5 (PF0/OSC_IN)

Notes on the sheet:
3.3V output
Additional caps on VBUS
4937N (30V) can do 8A continuous current on minimal pad in thermal limit NVTFS5C658NL is a similar 60V part
12V output
3V3 loads STM32G4 AS5047 TMC6200 IO UART
V0.2: VBUS feedback
SPI on STM32G4 would need an inverter on SLCK because hardware NSS only works in Motorola Mode, but DRV8323 needs reverse CPOL
VDD can be 5V to 12V
USB-C in USB 2.0 compat mode but with Power Delivery

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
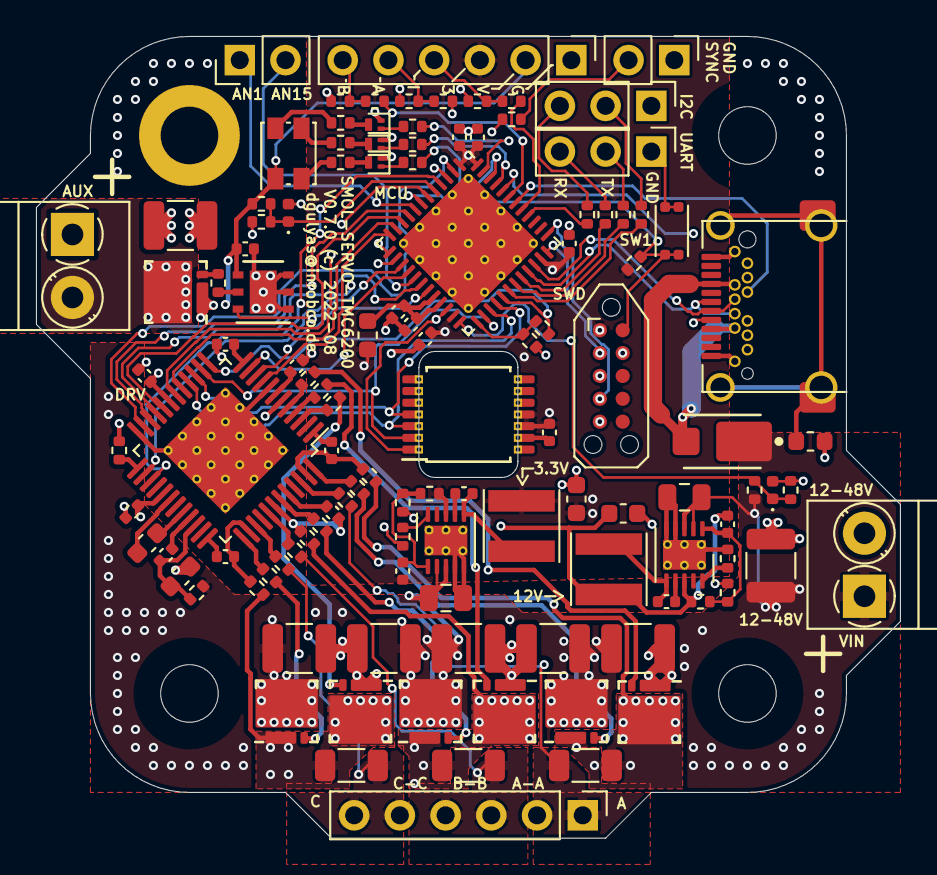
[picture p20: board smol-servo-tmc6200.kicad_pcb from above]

Board: 4 copper layers, 48.0 x 44.5 mm, 120 parts (0 on the bottom side), 109 nets.

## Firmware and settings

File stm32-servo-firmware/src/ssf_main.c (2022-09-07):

#include "stm32g4xx_hal.h"
#include "stm32g4xx_hal_adc.h"


#include "debug.h"

#include "main.h"
#include "ssf_main.h"
#include "ssf_spi.h"
#include "ssf_flash.h"
#include "ssf_mctrl.h"
#include "ssf_supervisor.h"
#include "utime.h"

#include "servo_hid_if.h"

#include <stdbool.h>
#include <stdio.h>
#include <errno.h>
#include <assert.h>

void __assert_func(const char * file, int line, const char * function, const char * expr)
{
	err_println("assertion failed: `%s` in %s, file %s:%u", expr, function, file, line);
	while (1) {};
}


static void _setPinAsGpioOutput(GPIO_TypeDef *gpio, uint32_t GPIO_Pin)
{
	// this works for single pins only
	uint32_t shift = (GPIO_Pin*GPIO_Pin);
	uint32_t modeMask = shift | (shift << 1);

	gpio->MODER = (gpio->MODER & ~modeMask) | (shift*0x01);
}

void test_chipSelects(void)
{
	_setPinAsGpioOutput(PIN_DRVSEL);
	_setPinAsGpioOutput(PIN_ASEL);
	// _setPinAsGpioOutput(PIN_SPI_NSS);

	// HAL_GPIO_WritePin(PIN_SPI_NSS, GPIO_PIN_RESET);
	// HAL_GPIO_WritePin(PIN_DRVSEL, GPIO_PIN_RESET);
	// HAL_GPIO_WritePin(PIN_ASEL, GPIO_PIN_RESET);
	// HAL_Delay(250);
	// HAL_GPIO_WritePin(PIN_DRVSEL, GPIO_PIN_SET);
	// HAL_Delay(250);
	// HAL_GPIO_WritePin(PIN_ASEL, GPIO_PIN_SET);
	// HAL_Delay(250);

	// HAL_GPIO_WritePin(PIN_SPI_NSS, GPIO_PIN_SET);
	// HAL_GPIO_WritePin(PIN_DRVSEL, GPIO_PIN_RESET);
	// HAL_GPIO_WritePin(PIN_ASEL, GPIO_PIN_RESET);
	// HAL_Delay(250);
	// HAL_GPIO_WritePin(PIN_DRVSEL, GPIO_PIN_SET);
	// HAL_Delay(250);
	// HAL_GPIO_WritePin(PIN_ASEL, GPIO_PIN_SET);
	// HAL_Delay(250);

	// HAL_GPIO_WritePin(PIN_SPI_NSS, GPIO_PIN_RESET);
	HAL_GPIO_WritePin(PIN_DRVSEL, GPIO_PIN_SET);
	HAL_GPIO_WritePin(PIN_ASEL, GPIO_PIN_RESET);
	HAL_Delay(50);
	HAL_GPIO_WritePin(PIN_ASEL, GPIO_PIN_SET);
	HAL_Delay(50);
	HAL_GPIO_WritePin(PIN_ASEL, GPIO_PIN_RESET);
	HAL_Delay(50);
	HAL_GPIO_WritePin(PIN_ASEL, GPIO_PIN_SET);
	HAL_Delay(50);

}

void spi_blockTest(void);

void ssf_init(void)
{
	do {dbg_println("ssf_init()...");} while (0);

	ssf_supervisorInit();
	utime_init();

	ssf_flashInit();

	// spi_blockTest();

	ssf_spiInit();

	ssf_ledInit();

	ssf_analogInit();
	// spwm_init();

	ssf_scheduleInit();


	mctrl_init();

	ssf_enableTasks(SCHED_UI_SLOW, SCHED_UI_SLOW, true);
}

/*
	FIXME: for some reason, calling fread() does not work right. _read is called only once, and never again, but calling _read() directly works as expected. This is a hack until it we figure out why stdio functions don't work. Writing, OTOH, appears to work just fine through fprintf().
*/
extern int _read(int32_t file, uint8_t *ptr, int32_t len);

static int _usbRead(void *ptr, size_t len)
{
	return _read(0, ptr, len);
}


char _usbcmd = 0;
static void _processUsbRx(void)
{
	// fprintf(stdout, "USB yay %u\r\n", HAL_GetTick());
	// _usbcmd = myRead();
	int readResult = _usbRead(&_usbcmd, 1);
	// dbg_println("fread() = %u, errno = %d", readResult, errno);
	if (readResult == 1)
	{
		// fwrite(&_usbcmd,1,1,stdout);

		// dbg_println("received something USB");
		switch (_usbcmd)
		{
			case 'b':
			{
				printf("Creating BLDC motor config...\r\n");

				device_config_t conf = {
					.blockInfo = { .flags = FLASH_CONFIG_TYPE_DEVICECONF_V1 },
					.userParams = {
						.ratedCurrent_A = 1.61f,
						.peakCurrent_A = 4.6f,
						.torqueConstant_Nm_per_A = 0.18f/4.6f,
						.rotorInertia_kgm2 = 24.0e-6f,
						.senseResistance_Ohm = 0.015f,
					},
				};

				ssf_flash_tryWriteBlock(
					conf.blockInfo.flags, 
					((uintptr_t)&conf) + sizeof(conf.blockInfo), 
					sizeof(conf) - sizeof(conf.blockInfo)
				);

				break;
			}
			case 'c':
			{
				printf("Clearing config flash...\r\n");
				ssf_flash_clearConfigFlash();
				printf("... clearing config flash done.\r\n");

				break;
			}
			case 'h':
			{
				printf("**** N17-SERVO HELP ****\r\n");
				printf("The following commands are available:\r\n");
				printf("  i - reset motor driver and parameter identification\r\n");
				printf("  b - create 42BLF01 BLDC motor config\r\n");
				printf("  r - reset MCU\r\n");
				printf("  c - clear config flash\r\n");
				break;
			}
			case 'i':
			{
				printf("Resetting Motor Driver...\r\n");
				mctrl_init();
				break;
			}
			case 'r':
			{
				printf("Resetting...\r\n");
				printf("3...\r\n");
				printf("2...\r\n");
				printf("1...\r\n");
				NVIC_SystemReset();
				break;
			}
			default:
			{
				dbg_println("received %u through USB", _usbcmd);
				break;
			}
		}
		_usbcmd = 0;		
	}

}

void ssf_usbRxCallback(const void* _data, size_t datalen)
{
	const char* str = _data;
	dbg_println("USB RX");
	if (datalen > 0)
	{
		_usbcmd = str[0];
	}
}

// static volatile sspi_as5047_state_t _hallState;
// static volatile uint32_t			_hallReadCounter;

// void ssf_asyncReadHallSensorCallback(sspi_as5047_state_t sensorState)
// {
// 	_hallState = sensorState;
// 	++_hallReadCounter;
// }

// float ssf_getEncoderAngle(void)
// {
// 	return (float)(_hallState.ANGLEUNC & 0x3FFF) / (float)0x4000 * 2.0f*M_PI;
// }


void ssf_ui1sTask(uint32_t now_us)
{
	// dbg_println("Hello USB!");
	// // HAL_Delay(8);
	
	// spi_printTransferStatus();
	// ssf_asyncReadHallSensor();
	// sspi_as5047_state_t hallState = ssf_readHallSensor();
	sspi_as5047_state_t hallState = ssf_dbgGetLastEncoderReading();
	// uint32_t readCounter = ssf_dbgGetEncoderReadCounter();
	// uint32_t formatErrorCounter = 0, valueErrorCounter = 0;
	// uint32_t errorCounter = ssf_dbgGetEncoderErrorCounter(&formatErrorCounter, &valueErrorCounter);
	// dbg_println("AS5047D %8u reads, %8u errors (%8u fmt, %8u val)", readCounter, errorCounter, formatErrorCounter, valueErrorCounter);

	ssf_dbgPrintEncoderStatus(hallState);
	// dbg_println("HALL[%8u] 0x%04x, 0x%04x, 0x%04x, 0x%04x", readCounter, hallState.NOP, hallState.ERRFL, hallState.DIAAGC, hallState.ANGLEUNC);
	if (0)
	{
		sspi_drv_state_t drvState = sspi_drv_readMotorDriver();
		// dbg_println("DRV %04x, %04x, %04x, %04x, %04x, %04x, %04x", drvState.FAULT_STATUS.reg, drvState.VGS_STATUS.reg, drvState.DRV_CTRL.reg, drvState.DRV_HS.reg, drvState.DRV_LS.reg, drvState.OCP_CTRL.reg, drvState.CSA_CTRL.reg);
		ssf_printMotorDriverFaults(drvState);
	}
	// // HAL_Delay(8);

	// bool drven = HAL_GPIO_ReadPin(PIN_DRVEN);
	// dbg_println("DRVEN %8u %u", utime_now(), drven);

	// uint32_t adcState = HAL_ADC_GetState(&hadc2);
	// uint32_t adcError = HAL_ADC_GetError(&hadc2);
	// dbg_println("ADC2 0x%08x, 0x%08x", adcState, adcError);
	// HAL_Delay(8);

	// dbg_println("iA = %8.3f %8.3f, iB = %8.3f %8.3f, iC = %8.3f %8.3f", (double)currentSensed[0], (double)currentSensed[1], (double)currentSensed[2], (double)currentSensed[3], (double)currentSensed[4], (double)currentSensed[5]);
	// dbg_println("iA = %5u %5u, iB = %5u %5u, iC = %5u %5u", (int)an1_buf[0], (int)an1_buf[1], (int)an1_buf[2], (int)an1_buf[3], (int)an1_buf[4], (int)an1_buf[5]);

	mctrl_simplePositionEstimate_t posEst = mctrl_getSimpleMotorPositionEstimate();

	dbg_println("x_est %8.3f deg, speed = %8.3f rpm", (double)(posEst.x[0][0]*180.0f/M_PI), (double)(posEst.x[1][0]*30.0f/M_PI));
	// mctrl_dbgPrintSimpleEstimatePair();
	// dbg_println("P =  %8.3g %8.3g", (double)(sqrtf(posEst.P[0][0])), (double)(sqrtf(posEst.P[0][1])));
	// dbg_println("     %8.3g %8.3g", (double)(sqrtf(posEst.P[1][0])), (double)(sqrtf(posEst.P[1][1])));
	// dbg_println("Q =  %8.3g %8.3g", (double)(sqrtf(posEst.debug.Q[0][0])), (double)(sqrtf(posEst.debug.Q[0][1])));
	// dbg_println("     %8.3g %8.3g", (double)(sqrtf(posEst.debug.Q[1][0])), (double)(sqrtf(posEst.debug.Q[1][1])));
	// dbg_println("K =  %8.3g", (double)((posEst.debug.K[0][0])));
	// dbg_println("     %8.3g", (double)((posEst.debug.K[1][0])));
	// dbg_println("R =  %8.3g", (double)(sqrtf(posEst.debug.R)));
	// dbg_println("t =  %8.3f, tm = %8.3f", (double)(1.0e-6f*posEst.timeStamp_us), (double)(1.0e-6f*posEst.lastMeasurementTimeStamp_us));

	dbg_println("VBUS = %.3f, VDDA = %.3f, VDDP = %.3f", (double)ssf_getVbus(), (double)ssf_getVdda(), (double)ssf_getVddp());


	// float* phaseCurrents0 = mctrl_getPhaseTable(2);
	// float* phaseCurrents1 = mctrl_getPhaseTable(3);

	// float maxi = 0.0f;
	// for (size_t i = 0; i < 16; ++i)
	// {
	// 	maxi = fmaxf(maxi, fabsf(phaseCurrents0[i]));
	// }

	// const char* padding = "                                ";
	// const char* line 	= "--------------------------------";


	// for (size_t i = 0; i < 16; ++i)
	// {
	// 	int lineLen = fminf(32.0f, 32.0f/maxi*fabsf(phaseCurrents0[i]));
	// 	int padLen = phaseCurrents0[i] > 0.0f ? 32 : 32-lineLen;
	// 	dbg_println("IB[%2u] = %8.3f, %8.3f %.*s%.*s", i, (double)phaseCurrents0[i], (double)phaseCurrents1[i], padLen, padding, lineLen, line);
	// }


}


void ssf_idle(void)
{
	ssf_ledIdle();

	mctrl_idle(utime_now());


	_processUsbRx();

	uint32_t now_ms = HAL_GetTick();

	servo_hid_interface_run(now_ms);

	// spwm_idle();
	// HAL_Delay(1);

	// ssf_asyncReadHallSensor();

	ssf_scheduleTasks(SCHED_UI_SLOW, SCHED_UI_SLOW, utime_now());

	// test_chipSelects();

}



static volatile int irqDummyCounter;

void WWDG_IRQHandler(void)
{
	// uart_printf("WWDG_IRQHandler!\r\n");
	while (1) {++irqDummyCounter;};
}

void PVD_PVM_IRQHandler(void)
{
	// uart_printf("WWDG_IRQHandler!\r\n");
	while (1) {++irqDummyCounter;};
}


void RTC_TAMP_LSECSS_IRQHandler(void)
{
	// uart_printf("WWDG_IRQHandler!\r\n");
	while (1) {++irqDummyCounter;};
}


void RTC_WKUP_IRQHandler(void)
{
	// uart_printf("WWDG_IRQHandler!\r\n");
	while (1) {++irqDummyCounter;};
}

// void FLASH_IRQHandler(void)
// {
// 	// uart_printf("WWDG_IRQHandler!\r\n");
// 	while (1) {++irqDummyCounter;};
// }

void RCC_IRQHandler(void)
{
	// uart_printf("WWDG_IRQHandler!\r\n");
	while (1) {++irqDummyCounter;};
}

void EXTI0_IRQHandler(void)
{
	// uart_printf("WWDG_IRQHandler!\r\n");
	while (1) {++irqDummyCounter;};
}


void EXTI1_IRQHandler(void)
{
	// uart_printf("WWDG_IRQHandler!\r\n");
	while (1) {++irqDummyCounter;};
}


void EXTI2_IRQHandler(void)
{
	// uart_printf("WWDG_IRQHandler!\r\n");
	while (1) {++irqDummyCounter;};
}


void EXTI3_IRQHandler(void)
{
	// uart_printf("WWDG_IRQHandler!\r\n");
	while (1) {++irqDummyCounter;};
}


void EXTI4_IRQHandler(void)
{
	// uart_printf("WWDG_IRQHandler!\r\n");
	while (1) {++irqDummyCounter;};
}

void DMA1_Channel3_IRQHandler(void)
{
	// uart_printf("WWDG_IRQHandler!\r\n");
	while (1) {++irqDummyCounter;};
}


void DMA1_Channel4_IRQHandler(void)
{
	// uart_printf("WWDG_IRQHandler!\r\n");
	while (1) {++irqDummyCounter;};
}


void DMA1_Channel5_IRQHandler(void)
{
	// uart_printf("WWDG_IRQHandler!\r\n");
	while (1) {++irqDummyCounter;};
}


void DMA1_Channel6_IRQHandler(void)
{
	// uart_printf("WWDG_IRQHandler!\r\n");
	while (1) {++irqDummyCounter;};
}

// void ADC1_2_IRQHandler(void)
// {
// 	// uart_printf("WWDG_IRQHandler!\r\n");
// 	while (1) {++irqDummyCounter;};
// }


// void USB_HP_IRQHandler(void)
// {
// 	// uart_printf("WWDG_IRQHandler!\r\n");
// 	while (1) {++irqDummyCounter;};
// }


// void USB_LP_IRQHandler(void)
// {
// 	// uart_printf("WWDG_IRQHandler!\r\n");
// 	while (1) {++irqDummyCounter;};
// }

void FDCAN1_IT0_IRQHandler(void)
{
	// uart_printf("WWDG_IRQHandler!\r\n");
	while (1) {++irqDummyCounter;};
}

void FDCAN1_IT1_IRQHandler(void)
{
	// uart_printf("WWDG_IRQHandler!\r\n");
	while (1) {++irqDummyCounter;};
}

void EXTI9_5_IRQHandler(void)
{
	// uart_printf("WWDG_IRQHandler!\r\n");
	while (1) {++irqDummyCounter;};
}

void TIM1_BRK_TIM15_IRQHandler(void)
{
	// uart_printf("WWDG_IRQHandler!\r\n");
	while (1) {++irqDummyCounter;};
}

// void TIM1_UP_TIM16_IRQHandler(void)
// {
// 	// uart_printf("WWDG_IRQHandler!\r\n");
// 	while (1) {++irqDummyCounter;};
// }

void TIM1_TRG_COM_TIM17_IRQHandler(void)
{
	// uart_printf("WWDG_IRQHandler!\r\n");
	while (1) {++irqDummyCounter;};
}

void TIM1_CC_IRQHandler(void)
{
	// uart_printf("WWDG_IRQHandler!\r\n");
	while (1) {++irqDummyCounter;};
}

void TIM2_IRQHandler(void)
{
	// uart_printf("WWDG_IRQHandler!\r\n");
	while (1) {++irqDummyCounter;};
}


void TIM3_IRQHandler(void)
{
	// uart_printf("WWDG_IRQHandler!\r\n");
	while (1) {++irqDummyCounter;};
}


void TIM4_IRQHandler(void)
{
	// uart_printf("WWDG_IRQHandler!\r\n");
	while (1) {++irqDummyCounter;};
}

void I2C1_EV_IRQHandler(void)
{
	// uart_printf("WWDG_IRQHandler!\r\n");
	while (1) {++irqDummyCounter;};
}

void I2C1_ER_IRQHandler(void)
{
	// uart_printf("WWDG_IRQHandler!\r\n");
	while (1) {++irqDummyCounter;};
}

void I2C2_EV_IRQHandler(void)
{
	// uart_printf("WWDG_IRQHandler!\r\n");
	while (1) {++irqDummyCounter;};
}

void I2C2_ER_IRQHandler(void)
{
	// uart_printf("WWDG_IRQHandler!\r\n");
	while (1) {++irqDummyCounter;};
}

void SPI1_IRQHandler(void)
{
	// uart_printf("WWDG_IRQHandler!\r\n");
	while (1) {++irqDummyCounter;};
}

// void SPI2_IRQHandler(void)
// {
// 	// uart_printf("WWDG_IRQHandler!\r\n");
// 	while (1) {++irqDummyCounter;};
// }

// void USART1_IRQHandler(void)
// {
// 	// uart_printf("WWDG_IRQHandler!\r\n");
// 	while (1) {++irqDummyCounter;};
// }

void USART2_IRQHandler(void)
{
	// uart_printf("WWDG_IRQHandler!\r\n");
	while (1) {++irqDummyCounter;};
}

void USART3_IRQHandler(void)
{
	// uart_printf("WWDG_IRQHandler!\r\n");
	while (1) {++irqDummyCounter;};
}

void EXTI15_10_IRQHandler(void)
{
	// uart_printf("WWDG_IRQHandler!\r\n");
	while (1) {++irqDummyCounter;};
}

void RTC_Alarm_IRQHandler(void)
{
	// uart_printf("WWDG_IRQHandler!\r\n");
	while (1) {++irqDummyCounter;};
}

void USBWakeUp_IRQHandler(void)
{
	// uart_printf("WWDG_IRQHandler!\r\n");
	while (1) {++irqDummyCounter;};
}


void TIM8_BRK_IRQHandler(void)
{
	// uart_printf("WWDG_IRQHandler!\r\n");
	while (1) {++irqDummyCounter;};
}


void TIM8_UP_IRQHandler(void)
{
	// uart_printf("WWDG_IRQHandler!\r\n");
	while (1) {++irqDummyCounter;};
}


void TIM8_TRG_COM_IRQHandler(void)
{
	// uart_printf("WWDG_IRQHandler!\r\n");
	while (1) {++irqDummyCounter;};
}


void TIM8_CC_IRQHandler(void)
{
	// uart_printf("WWDG_IRQHandler!\r\n");
	while (1) {++irqDummyCounter;};
}

void LPTIM1_IRQHandler(void)
{
	// uart_printf("WWDG_IRQHandler!\r\n");
	while (1) {++irqDummyCounter;};
}


void SPI3_IRQHandler(void)
{
	// uart_printf("WWDG_IRQHandler!\r\n");
	while (1) {++irqDummyCounter;};
}


void UART4_IRQHandler(void)
{
	// uart_printf("WWDG_IRQHandler!\r\n");
	while (1) {++irqDummyCounter;};
}


void TIM6_DAC_IRQHandler(void)
{
	// uart_printf("WWDG_IRQHandler!\r\n");
	while (1) {++irqDummyCounter;};
}


void TIM7_IRQHandler(void)
{
	// uart_printf("WWDG_IRQHandler!\r\n");
	while (1) {++irqDummyCounter;};
}


// void DMA2_Channel1_IRQHandler(void)
// {
// 	// uart_printf("WWDG_IRQHandler!\r\n");
// 	while (1) {++irqDummyCounter;};
// }


// void DMA2_Channel2_IRQHandler(void)
// {
// 	// uart_printf("WWDG_IRQHandler!\r\n");
// 	while (1) {++irqDummyCounter;};
// }


void DMA2_Channel3_IRQHandler(void)
{
	// uart_printf("WWDG_IRQHandler!\r\n");
	while (1) {++irqDummyCounter;};
}


void DMA2_Channel4_IRQHandler(void)
{
	// uart_printf("WWDG_IRQHandler!\r\n");
	while (1) {++irqDummyCounter;};
}


void DMA2_Channel5_IRQHandler(void)
{
	// uart_printf("WWDG_IRQHandler!\r\n");
	while (1) {++irqDummyCounter;};
}


void UCPD1_IRQHandler(void)
{
	// uart_printf("WWDG_IRQHandler!\r\n");
	while (1) {++irqDummyCounter;};
}


void COMP1_2_3_IRQHandler(void)
{
	// uart_printf("WWDG_IRQHandler!\r\n");
	while (1) {++irqDummyCounter;};
}


void COMP4_IRQHandler(void)
{
	// uart_printf("WWDG_IRQHandler!\r\n");
	while (1) {++irqDummyCounter;};
}


void CRS_IRQHandler(void)
{
	// uart_printf("WWDG_IRQHandler!\r\n");
	while (1) {++irqDummyCounter;};
}


void SAI1_IRQHandler(void)
{
	// uart_printf("WWDG_IRQHandler!\r\n");
	while (1) {++irqDummyCounter;};
}


void FPU_IRQHandler(void)
{
	// uart_printf("WWDG_IRQHandler!\r\n");
	while (1) {++irqDummyCounter;};
}


void RNG_IRQHandler(void)
{
	// uart_printf("WWDG_IRQHandler!\r\n");
	while (1) {++irqDummyCounter;};
}


void LPUART1_IRQHandler(void)
{
	// uart_printf("WWDG_IRQHandler!\r\n");
	while (1) {++irqDummyCounter;};
}


// void I2C3_EV_IRQHandler(void)
// {
// 	// uart_printf("WWDG_IRQHandler!\r\n");
// 	while (1) {++irqDummyCounter;};
// }


// void I2C3_ER_IRQHandler(void)
// {
// 	// uart_printf("WWDG_IRQHandler!\r\n");
// 	while (1) {++irqDummyCounter;};
// }


void DMAMUX_OVR_IRQHandler(void)
{
	// uart_printf("WWDG_IRQHandler!\r\n");
	while (1) {++irqDummyCounter;};
}


void DMA2_Channel6_IRQHandler(void)
{
	// uart_printf("WWDG_IRQHandler!\r\n");
	while (1) {++irqDummyCounter;};
}


void CORDIC_IRQHandler(void)
{
	// uart_printf("WWDG_IRQHandler!\r\n");
	while (1) {++irqDummyCounter;};
}


void FMAC_IRQHandler(void)
{
	// uart_printf("WWDG_IRQHandler!\r\n");
	while (1) {++irqDummyCounter;};
}

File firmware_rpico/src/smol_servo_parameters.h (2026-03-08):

#pragma once

/**
 * 3 phase servo loop sketch
 * 
 * LOOP ...  t=0                                             t=1...
 * 20k       |                                               |
 * PWM  ...  0               1               2               0  ...
 * 60k       |               |               |               |
 * MAG  ...  0           1           2           3           0  ...
 * 80k       |           |           |           |           |
 * ADC  ... 0.0 0.1 0.2 0.3 1.0 1.1 1.2 1.3 2.0 2.1 2.2 2.3 0.0 ... 
 * 240k     |   |   |   | : |   |   |   | : |   |   |   | : |
 * ADC-IRQ                x               x               x 
 * 
 * The LOOP IRQ is driven by signaling from the PWM callback, but ADC and MAG run independent PWM channels.
 * 
 * The startup phase is interesting to get the callbacks aligned:
 * PWM            >               0               1      ...
 * 60k            >               |               |
 * MAG            >   3   .   .   0           1          ...
 * 80k            >~~~|           |           |        
 * ADC (-1us)     >  2.1 2.2 2.3 0.0 0.1 0.2 0.3 1.0 1.1 ... 
 * 240k           >~~|   |   | : |   |   |   | : |   |
 * ADC-IRQ                     x               x            
 * 
 * [squiggly "~" line means shortened COUNT to align phases]
 * 
 * - ADC triggering has a -1us offset because sampling takes 2us, and we want to be centered on the PWM wrap as the primary tick. For starting out, to have the 1:4 ADC-IRQ align correctly with the PWM, the first "block" is only 3 ADC reads, then is switched to 4.
 *   - `-1us` offset for ADC read
 *   - 3 vs 4 reads in first block
 *   - start at N-1 phase for the IRQ
 * - MAG is a slightly shorter period than PWM, so we need to 
 *   - offset to align zero phases of PWM and MAG
 *   - start at N-1 phase of buffers
 * 
 * 
 */

#define SMOL_SERVO_PHASES                   (3)
#define SMOL_SERVO_PWM_PER_LOOP             (3)

#define SMOL_SERVO_LOOP_FREQ_HZ             (20000)
#define SMOL_SERVO_LOOP_PERIOD_CLOCKS       (7500)

#define SMOL_SERVO_BRIDGE_PWM_FREQ_HZ       (60000)
#define SMOL_SERVO_BRIDGE_PWM_PERIOD_CLOCKS (2500)

#define SMOL_SERVO_ADC_FREQ_HZ              (240000)
#define SMOL_SERVO_ADC_PERIOD_CLOCKS        (625)

#define SMOL_SERVO_ADC_ADVANCE_COUNT        (150)

#define SMOL_SERVO_MAG_PWM_PER_LOOP         (4)
#define SMOL_SERVO_MAG_FREQ_HZ              (80000)
#define SMOL_SERVO_MAG_PERIOD_CLOCKS        (1875)

#define SMOL_SERVO_PWM_SLICE_MASK ((1u << PWMA_SLICE) | (1u << PWMB_SLICE) | (1u << PWMC_SLICE) | (1u << PWMR_SLICE) | (1u << PWM_ADC_SLICE) | (1u << PWM_SERVO_LOOP_SLICE) | (1u << PWM_DOUBLETIME_SLICE) | (1u << PWM_MAG_SLICE))
// #define SMOL_SERVO_PWM_SLICE_MASK (0xFFFFFFFF)

#define BRIDGE_PWM_WRAP_IRQ PWM_IRQ_WRAP_0
#define ADC_IRQ ADC_IRQ_FIFO

// current sense resistors
#define ISENSE_R (5.0e-3f)
// TMC6200 amplifier settings
#define ISENSE_AMPLIFICATIONS {5.0f, 10.0f, 10.0f, 20.0f}
// THE TMC6200 is using its own 5V regulator, so measured ZERO is expected to vary because the ADC VDD is an independent rail.
#define VSENSE_NOMINAL_ZERO_V (5.0f/3.0f)
#define VSENSE_ZERO_V_INIT_VARIANCE (0.1f*0.1f)
// 10mV/sec
#define VSENSE_ZERO_V_UPDATE_VARIANCE (0.01f*0.01f)

#define ADC_REF_VOLTAGE (3.3f)
#define ADC_REF_RESISTANCE (100.0e6f)
#define ADC_DIV_LEG_R (5.1e3f)
// consider ADC resistance to R1 of voltage divider
/**
 * VX_-----------o---------
 *               |
 *             [R_2]
 *               |
 * VSENSE-o------o------.
 *        |      |      |
 *     [R_ADC] [R_1] [Z 3.3V]
 *        |      |      |
 * GND_---o------o------o--
 * 
 * VSENSE = VX * (R_1 || R_ADC) / ((R_1 || R_ADC) + R_2)
 * 
 */
#define ADC_DIV_COMBO ((ADC_DIV_LEG_R * ADC_REF_RESISTANCE) / (ADC_DIV_LEG_R + ADC_REF_RESISTANCE))
#define ADC_VDD_DIV (ADC_DIV_COMBO / (22.0e3f + ADC_DIV_COMBO))
#define ADC_VBUS_DIV (ADC_DIV_COMBO / (120.0e3f + ADC_DIV_COMBO))

// NOTE: on ARM, the IRQ group.subgroup is configured via the AICR's PRIGROUP field. The default is a single bit for subgroup, rest group.
// Since the RP2350 only implements the top 4 bits, this should mean we have 16 priority levels with no subpriority selection.
#define SMOL_ADC_IRQ_PRIORITY  (0x10)
#define SMOL_PWM_IRQ_PRIORITY  (0x20)
#define SMOL_LOOP_IRQ_PRIORITY (0x80)

#define DEBUG_LOOP_IRQ_WITH_GPIO 8
#define DEBUG_ADC_TIMING_WITH_GPIO 9
#define DEBUG_PWM_IRQ_WITH_GPIO 13
// #define DEBUG_PWM_ADC_IRQ
// #define DEBUG_PWM_ADC_GPIO 28
// #define DEBUG_DMA_ADC
// #define DEBUG_ADC_FIFO_THRES
#define DEBUG_ADC_FIFO_THRES_WITH_GPIO 12

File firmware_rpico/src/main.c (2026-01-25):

/**
 * 
 */

#include <stdio.h>

#include "pico/stdlib.h"
#include "pico/binary_info.h"
#include "pico/critical_section.h"
#include "pico/multicore.h"

#include "hardware/i2c.h"
#include "hardware/structs/busctrl.h"
#include "hardware/structs/accessctrl.h"

#include "smol_servo.h"
#include "smol_fs.h"
#include "smol_console.h"
#include "pico_debug.h"

#include "fusb302.h"
#include "tmc6200.h"


void i2c_fusb_init(void) {
    i2c_init(FUSB_I2C, 100 * 1000);
    gpio_set_function(FUSB_I2C_SDA_PIN, GPIO_FUNC_I2C);
    gpio_set_function(FUSB_I2C_SCL_PIN, GPIO_FUNC_I2C);
    gpio_pull_up(FUSB_I2C_SDA_PIN);
    gpio_pull_up(FUSB_I2C_SCL_PIN);
    // Make the I2C pins available to picotool
    bi_decl(bi_2pins_with_func(FUSB_I2C_SDA_PIN, FUSB_I2C_SCL_PIN, GPIO_FUNC_I2C));

}

void smol_hires_time_init(void) {
	// use a critical section to block IRQs, at least
	// this should not be called once the second core is up
	critical_section_t cr;
	critical_section_init(&cr);
	critical_section_enter_blocking(&cr);
	timer_hw_t *timer_us = timer0_hw;
	timer_hw_t *timer_sysclk = timer1_hw;



	// pause timers
	bool was_paused = timer_us->pause;
	timer_us->pause = 1;
	timer_sysclk->pause = 1;

	// set 2nd timer to sysclk
	timer_sysclk->source = 1;
	// set time to match 1MHz timer
	uint64_t time_us = timer_us->timelr;
	time_us = (time_us << 32) | timer_us->timehr;
	// looking at runtime_init_clocks(), default is 150MHz, we'll just go with that
	uint64_t time_sysclk = time_us * 150u;
	timer_sysclk->timelw = time_sysclk;
	timer_sysclk->timehw = time_sysclk >> 32;

	// unpause both timers with hopefully negligible delay
	timer_us->pause = was_paused;
	timer_sysclk->pause = was_paused;

	critical_section_exit(&cr);
	critical_section_deinit(&cr);
}

#define LED_PIN 8

// Initialize the GPIO for the LED
void pico_led_init(void) {
    // A device like Pico that uses a GPIO for the LED will define PICO_DEFAULT_LED_PIN
    // so we can use normal GPIO functionality to turn the led on and off
    gpio_init(LED_PIN);
    gpio_set_dir(LED_PIN, GPIO_OUT);
}

// Turn the LED on or off
void pico_set_led(bool led_on) {
    // Just set the GPIO on or off
    gpio_put(LED_PIN, led_on);
}

static void __not_in_flash_func(_core1_init)(void) {
	// // mess with AHB priorities
	// uint32_t prio = busctrl_hw->priority;
	// // increase Core1 bus priority
	// prio = BUSCTRL_BUS_PRIORITY_PROC1_BITS;
	// busctrl_hw->priority = prio;

	smol_servo_loop_init();
	// smol_servo_loop_start();


	// disable FLASH access for CORE 1 so we don't get XIP data stalls
	hw_clear_bits(&accessctrl_hw->xip_main, 0xACCE0000 | ACCESSCTRL_XIP_MAIN_CORE1_BITS);

	while (1) {
		smol_servo_loop_idle_core1();
	}
}

int main(int argc, char const *argv[])
{
	smol_hires_time_init();

    stdio_init_all();
    pico_led_init();

    smol_fs_init();

    // Make the SPI pins available to picotool
    bi_decl(bi_3pins_with_func(DRV_MISO_PIN, DRV_MOSI_PIN, DRV_SLCK_PIN, GPIO_FUNC_SPI));
    // Make the CS pin available to picotool
    bi_decl(bi_1pin_with_name(DRV_NSS_PIN, "DRV_SPI CS"));

    tmc6200_spi_init(DRV_SPI, DRV_MOSI_PIN, DRV_NSS_PIN, DRV_SLCK_PIN, DRV_MISO_PIN);

	i2c_fusb_init();
	fusb302_init(FUSB_I2C, FUSB_INT_PIN);
	smol_usb_pd_init();

	multicore_reset_core1();
	multicore_launch_core1(_core1_init);

	bool led = false;
	while (1) {
		picobug_process_core1_queue();

		int ch = getchar_timeout_us(0);
		if (ch >= 0) {
			smol_console_process_char(ch);
		}

		smol_usb_pd_run();

		smol_servo_loop_idle_core0();

		// pico_set_led(led = !led);
		// uint64_t t_fast = timer_time_us_64(timer1_hw);
		// dbg_time_t tt = {.seconds = t_fast / 1000000u, .microseconds = t_fast % 1000000u};
		// dbg_println("foo %" PRIu32 ".%06" PRIu32, tt.seconds, tt.microseconds);
		// sleep_ms(1000);
		// printf("foo\n");
	}
	return 0;
}

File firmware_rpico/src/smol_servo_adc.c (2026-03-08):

/**
 * smol-servo ADC setup
 * 
 * We're running up/down PWM at 60kHz (120kHz) and need to sample at both 0 and TOP+1 counts.
 * 
 * However, the PWM module only allows DMA requests on counter wrap, so we have to setup a spare PWM or other timer mechanism.
 * 
 * An ADC samples takes 2us, so we should trigger 1us before counter wrap (150 cycles).
 * 
 * NOTE: it may be possible to use a "negative" counter value instead of retarding the PWM counter by 150 cycles from software to get the correct phase alignment.
 * 
 * Additionally, we should interleave the 120kHz 3-phase current reads with
 * the voltage and auxiliary sensors. We have a total of 9 channels anyway,
 * might as well make use of it.
 * 
 *  0    TOP    0    TOP    0    TOP   :0 
 *  |     |     |     |     |     |    :|  ...
 *  I0    I0    I1    I1    I2    I2   :I0
 *     V0    V1    V2   VDIV  VBUS  TEMP
 * 
 * Thus the order of channels:
 * 0,3, 0,4, 1,5, 1,6, 2,7, 2,8
 * 
 * This would result in a 240kHz sample rate. We could insert additional reads to denoise the non-current sense reads:
 * 0,3,3,3, 0,4,4,4, 1,5,5,5, 1,6,6,6, 2,7,7,7, 2,8,8,8
 *
 * It does not make sense to increase the number of current sense reads because of potential switching noise. The current sense points are at 0 and TOP, so one of the two is picked depending on proximity of the switching time. One will always be relatively far away, the other closer (until we get to "step" speeds where polarity switches each PWM period)
 * 
 * What makes sense to set up? 120kHz is 1250 cycles, 240kHz is 625 cycles. Since we don't have an integer number of cycles to go higher, we'd have to feed the PWM TOP with 312/313 alternatingly. One option is to setup a DMA for TOP that, the other could be to use PH_RET to retard it by one cycle every other period.
 * 
 * If we feed TOP, we can do DMA chaining to trigger the ADC.
 * 
 * Going with 240kHz, we do not need to alternate counts.
 * 
 * We also have the 8 entry ADC FIFO, so don't need to do DMAs as long as we read out the FIFO often enough.
 * 
 * We'll start with 240kHz ADC reads for simplicity. DMA to ADC.CS will trigger ADC reads.
 * 
 * PWM[6].WRAP --.
 *               |
 *               V
 * CS_RINGBUF -> DMA -> ADC.CS -> ADC.READ -.
 *                                          |
 *                                        1 / 4
 *                                          |
 *                                          V
 *                            ADC.FCS -> adc_fifo_threshold_irq()
 *                                             
 * 
 * 
 */

#include "smol_servo.h"
#include "smol_servo_parameters.h"
#include "smol_fast.h"
#include "pico_debug.h"

#include "hardware/platform_defs.h"
#include "hardware/dma.h"
#include "hardware/adc.h"
#include "hardware/pwm.h"

#include <stdint.h>
#include <string.h>
#include <assert.h>

// 4 ADC reads for every interrupt 
#define ADC_PATTERN_BLOCK_SIZE 4
#define ADC_PATTERN_NUM_BLOCKS 3

#define ADC_RINGBUF_NUM_BLOCKS (4)
#define ADC_RINGBUF_WORDS (ADC_PATTERN_BLOCK_SIZE*ADC_RINGBUF_NUM_BLOCKS)
#define ADC_RINGBUS_BITS (6)
_Static_assert((1 << ADC_RINGBUS_BITS) == (4 * ADC_RINGBUF_WORDS));

#define ADC_PWM_TOP (SMOL_SERVO_ADC_PERIOD_CLOCKS-1)

#define ADC_FIFO_THRESHOLD (4)
// start with N-1 for the first block to align correctly with bridge PWM
#define ADC_FIFO_STARTING_THRESHOLD (ADC_FIFO_THRESHOLD-1)

#define ADC_CHANNEL_VBUS (3)
#define ADC_CHANNEL_VDD (4)
#define ADC_CHANNEL_TEMPERATURE (8)

#define ADC_IRQ_PERIOD_CLOCKS_NOMINAL (ADC_FIFO_THRESHOLD*SMOL_SERVO_ADC_PERIOD_CLOCKS)
// allow a 2us deviation
#define ADC_IRQ_PERIOD_CLOCKS_ALLOWANCE (300)
#define ADC_IRQ_PERIOD_CLOCKS_MIN (ADC_IRQ_PERIOD_CLOCKS_NOMINAL - ADC_IRQ_PERIOD_CLOCKS_ALLOWANCE)
#define ADC_IRQ_PERIOD_CLOCKS_MAX (ADC_IRQ_PERIOD_CLOCKS_NOMINAL + ADC_IRQ_PERIOD_CLOCKS_ALLOWANCE)

static int __not_in_flash("ADC") _adc_irq_period_clocks_min = ADC_IRQ_PERIOD_CLOCKS_MIN;
static int __not_in_flash("ADC") _adc_irq_period_clocks_max = ADC_IRQ_PERIOD_CLOCKS_MAX;

static int _adc_cs_dma_channel = -1;

static uint32_t _block_index = ADC_PATTERN_NUM_BLOCKS - 1;
static uint32_t _ringbuf_index = 0;

static uint32_t _adc_cs_buf[ADC_PATTERN_NUM_BLOCKS][ADC_PATTERN_BLOCK_SIZE];

static uint32_t _adc_cs_ringbuf[ADC_RINGBUF_NUM_BLOCKS][ADC_PATTERN_BLOCK_SIZE] __attribute__((aligned(4*ADC_RINGBUF_WORDS)));

static volatile uint32_t _adc_read_buf[NUM_ADC_CHANNELS][2];
static volatile uint32_t _adc_time_buf[NUM_ADC_CHANNELS][2];

uint32_t smol_adc_block_index(void) {
	return _block_index;
}

static uint32_t _prev_irq_t_clocks = 0;

void __not_in_flash_func(smol_adc_fifo_threshold_irq_handler)(void) {
#ifdef DEBUG_ADC_FIFO_THRES_WITH_GPIO
	gpio_out_put_fast(DEBUG_ADC_FIFO_THRES_WITH_GPIO, 1);
#endif
	// we expect this to be called every ADC_FIFO_THRESHOLD samples
#ifdef DEBUG_ADC_FIFO_THRES
	dbg_println("adc fifo!");
#endif
	/**
	 * ADC block interrupt handler
	 * 
	 * store samples and times
	 */
	static bool is_first_run = true;

	uint32_t block_complete_index = _block_index;
	uint32_t ringbuf_complete_index = _ringbuf_index;

	uint32_t t_clocks = smol_time32(timer1_hw);
	uint32_t dt = t_clocks - _prev_irq_t_clocks;
	// Block of ADC reads has completed.
	// 1. Gather ADC reads
	// 2. Refill CS pattern ringbuf

	uint32_t prev_block_index = (block_complete_index + ADC_PATTERN_NUM_BLOCKS - 1) % ADC_PATTERN_NUM_BLOCKS;
	uint32_t next_block_index = (block_complete_index + 1) % ADC_PATTERN_NUM_BLOCKS;
	uint32_t next_ringbuf_index = (ringbuf_complete_index + 1) % ADC_RINGBUF_NUM_BLOCKS;

	if (is_first_run) {
		// let's see if this fixes the first run assert
		// NOTE: first run is N-1 entries we ignore.
		for (size_t i = 0; i < ADC_FIFO_STARTING_THRESHOLD; ++i) {
			volatile int val = adc_hw->fifo;
			// adc_fifo_get();
		}
		// update FIFO threshold
		uint32_t fcs = adc_hw->fcs;
		fcs = (fcs & ~ADC_FCS_THRESH_BITS) | (ADC_FIFO_THRESHOLD << ADC_FCS_THRESH_LSB);

		adc_hw->fcs = fcs;
		// *hw_set_alias(&adc_hw->fcs) = ADC_FCS_UNDER_BITS | ADC_FCS_OVER_BITS;
		assert_fast(0 == (fcs & ADC_FCS_OVER_BITS));
		assert_fast(0 == (fcs & ADC_FCS_UNDER_BITS));
		is_first_run = false;
	}
	else
	{
		assert_fast(dt > _adc_irq_period_clocks_min);
		assert_fast(dt < _adc_irq_period_clocks_max);
		// gather ADC read results from FIFO
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

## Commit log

2019-08-23 Initial commit of NEMA17 form factor servo driver
    [stm32-nema17-servo-B_Cu.gbl, stm32-nema17-servo-B_Mask.gbs, stm32-nema17-servo-B_Paste.gbp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]
2019-08-27 board layout improvements and firmware that finally shows up as USB CDC device
    [stm32-nema17-servo.kicad_pcb]
2019-08-27 move electronics design files into hardware/ folder
    [stm32-nema17-servo.kicad_pcb, stm32-nema17-servo.sch]
2019-09-08 initial commit of custom mechaduino firmware that boots with Arduino/SAM-BA bootloader
2019-09-10 working constant speed open loop mechaduino stepper driving at constant speed with an interpolated sine lookup
2019-09-11 further progress in bringing up SPI, ADCs, etc
2019-09-11 further fixes on v0.2 hardware
    [stm32-nema17-servo.kicad_pcb, stm32-nema17-servo.sch]
2019-09-17 hardware version 0.2 as sent to board fab
    [stm32-nema17-servo.kicad_pcb, stm32-nema17-servo.sch]
2019-09-18 further firmware improvements, including proper scheduling of fast control loop to sync with PWM/ADC and readout of the current feedback signals
2019-09-18 adds missing VREF connections on STM32 and DRV8323
    [stm32-nema17-servo.kicad_pcb, stm32-nema17-servo.sch]
2019-09-24 adds fuse to USB power input to protect both host and device
    [stm32-nema17-servo.kicad_pcb, stm32-nema17-servo.sch]
2019-09-24 motor parameter estimation can now be triggered from USB, and it estimates inductance on each phase via kalman filters
2020-03-31 software updated for V0.2 hardware, with characterization experiments; work on V0.3 hardware fixes
    [stm32-nema17-servo.kicad_pcb, stm32-nema17-servo.sch]
2020-04-01 initial commit for switch to 3rd party UsbDevice lib, so that we can have HID+CDC at the same time, which isn't easily possible with the STM32 library on STM32G4
2020-04-01 improved debug output, now also available over uart
2020-04-02 enable debug output over uart, it is more convenient for naw than through USB
2020-04-02 PCB layout improvements
    [stm32-nema17-servo.kicad_pcb, stm32-nema17-servo.sch]
2020-04-03 adds HID device with X axis RGB LED control
2020-04-03 more enhancements for v0.3, discovered that hardware NSS should be usable, after all
    [stm32-nema17-servo.kicad_pcb, stm32-nema17-servo.sch]
2020-04-07 hardware v0.3 as ordered
    [stm32-nema17-servo.kicad_pcb, stm32-nema17-servo.sch]
2020-04-09 hall sensor now read asynchronously
2020-04-12 fix erroneous timer period for gate driver PWM
    [main.c]
2020-04-13 current sense improvements: added more documentation and current sense sampling now centered on PWM phases through offset with TIM15
2020-04-13 SPI handling improvements to prevent race conditions
2020-04-22 disable USB init from HAL through ifdef in user code instead of comments, add TIM1 init as event counter, and fix ADC clock source
    [main.c]
2020-04-22 add TIM1 initialization as event counter for ADC triggering
2020-04-22 add function to enable motor driver half bridges individually
2020-04-22 improvements and experiments with system identification: added linear regression function, and fixed up some formulas
    [ssf_mctrl.c]
2020-04-23 add ADC sampling offset for current sensing
2020-04-23 adjust VBUS and VDDP readouts to compensate for parasitic resistances
2020-04-23 change system identification to use static method for resistance, and dynamic for impedance, as dynamic is terrible for impedance due to noise; add collect vbus readouts during identification in addi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
    [ssf_mctrl.c]
2020-04-23 cosmetic updates to schematic and board
    [stm32-nema17-servo.kicad_pcb, stm32-nema17-servo.sch]
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2020-04-24 add delay-less SPI NSS pulse timing with TIM16; refactor mctrl a bit
2020-04-24 start on framework for storing configuration data in flash
2020-04-25 had to add 'reset halt' to rst target to reliably restart MCU, otherwise it would sometimes get stuck in calibration, but the bug cannot be reproduced with the debugger attached
2020-04-25 add impedance based inductance estimation, which seems to give a better estimate than di/dt based
2020-04-26 fix ADC trigger offseting
2020-04-26 oversampling mode for ADC2 now set based on header macros, so we don't have through stm32cube codegen for changes
2020-04-26 add debug printf function to be able to output partial lines, for data mainly
2020-04-27 chang AS5047 NSS pin to start high on reset, enable OC preload for SPI timer
    [main.c]
2020-04-30 improved SPI state machine, though still not without quirks
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2020-04-30 added stall speed detection for identifying motor constants better
    [ssf_mctrl.c]
2020-06-02 v0.3.1 hardware doe not require parasitic correction due to 100n buffer caps
    [ssf_analog.c]
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2020-06-05 fix bug in SPI state machine that caused an SPI transfer to signal completion before all data was transfered, under certain conditions
2020-06-05 improved SPI API for bug hunting
    [ssf_main.c]
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2020-10-09 setting a power PWM channel now returns the integer value that was set in hardware
2020-10-09 improve SPI state machine by adding error recovery mechanism when attempting to start transfers
2020-10-09 improved encoder errors debugging; improved motor param estimation
    [ssf_mctrl.c]
2020-10-10 revert change for current calc function proto for now
    [ssf_mctrl.c]
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2020-10-28 adds cooldown phase for motor driver init errors; improvements for parameter detection
    [ssf_mctrl.c]
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2020-10-28 updated driver config with v1.3 HAL package, and some minor fixes in timer and ADC config
    [firmware48.ioc, main.c]
2020-10-28 squelch compiler warning by adding default case in switch for unknown channels
2020-10-28 more config flash impl improvements; fix page erase
    [ssf_flash.c, ssf_flash.h]
2020-10-28 fix missing var in page erase
    [ssf_flash.c, ssf_flash.h]
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2021-12-30 v0.3.1 board
    [stm32-nema17-servo.kicad_pcb, stm32-nema17-servo.sch]
2022-01-03 commits missing timer function prototypes in header
    [ssf_main.h]
2022-01-03 4 layer board design
    [stm32-nema17-servo.kicad_pcb]
2022-02-20 cosmetic updates to some of the pcb footprints, mainly for better 3D models
    [stm32-nema17-servo.kicad_pcb, stm32-nema17-servo.kicad_sch]
2022-02-26 tweaks to v0.4.0 hardware design
    [stm32-nema17-servo.kicad_pcb, stm32-nema17-servo.kicad_sch]
2022-08-06 addition of TMC6200 variant
    [smol-servo-tmc6200.kicad_pcb, smol-servo-tmc6200.kicad_sch, stm32-nema17-servo-drv8300_variant.kicad_sch]
2022-08-06 rearrange TMC6200 version to have MCU closer to driver chip
    [smol-servo-tmc6200.kicad_pcb, smol-servo-tmc6200.kicad_sch]
2022-08-06 v0.6.0 PCB order
    [smol-servo-tmc6200.kicad_pcb]
2022-08-21 v0.6.1 hardware
    [smol-servo-tmc6200.kicad_pcb, smol-servo-tmc6200.kicad_sch]
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2022-08-24 add v0.7.0 prelim hardware design with USB Power Delivery
    [smol-servo-tmc6200.kicad_pcb, smol-servo-tmc6200.kicad_sch]
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2022-08-26 work on tmc6200 bringup; spi reorg; start on cogging characterization
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2022-09-07 kalman filter impl; SPI improvements; analog readout improvements
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2024-08-22 smol-servo RPI2350B variant
    [RP2350_QFN60.step, RP2350_QFN80.step, smol-servo-rpi2350-tmc6200.kicad_pcb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]
2024-08-24 updated RP2350 hardware
    [smol-servo-rpi2350-tmc6200.kicad_pcb, smol-servo-rpi2350-tmc6200.kicad_sch]
2024-08-27 addition of USB-C reverse current protection
    [smol-servo-rpi2350-tmc6200.kicad_pcb, smol-servo-rpi2350-tmc6200.kicad_sch]
2025-10-05 change RP2350 board to JLCPCB spec as they are the only ones who have RP2354B chips at the moment
    [smol-servo-rpi2350-tmc6200.kicad_pcb, smol-servo-rpi2350-tmc6200.kicad_sch]
2025-12-28 RP2350 split board hardware
    [smol-servo-nomcu-tmc6200.kicad_pcb, smol-servo-nomcu-tmc6200.kicad_sch, smol-servo-rp-nodrv.kicad_pcb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]
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2026-01-20 v0.9.1 RP2350 fixes
    [smol-servo-rp-nodrv.kicad_pcb, smol-servo-rp-nodrv.kicad_sch, smol-servo-rpi2350-tmc6200.kicad_pcb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]
2026-01-20 USB PD related work (waiting for hardware fix)
    [fusb302.c]

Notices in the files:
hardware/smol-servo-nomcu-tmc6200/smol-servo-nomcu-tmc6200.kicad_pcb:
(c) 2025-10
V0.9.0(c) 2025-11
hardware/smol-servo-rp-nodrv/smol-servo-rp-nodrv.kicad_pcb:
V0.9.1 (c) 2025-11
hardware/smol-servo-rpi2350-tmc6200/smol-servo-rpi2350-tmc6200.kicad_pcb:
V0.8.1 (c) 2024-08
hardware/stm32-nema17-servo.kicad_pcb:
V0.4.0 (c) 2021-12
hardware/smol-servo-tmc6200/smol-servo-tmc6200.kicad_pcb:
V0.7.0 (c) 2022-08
